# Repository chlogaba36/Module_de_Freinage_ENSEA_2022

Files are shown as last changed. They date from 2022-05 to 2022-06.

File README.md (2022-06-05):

# Module_de_Freinage_ENSEA_2022


<h5>
Dans le cadre de projet de 1ère année à l'ENSEA, nous avons créé un frein pour moteur à courant continue reposant sur le principe de résitance dissipative.
Notre module est alimenté par la source de la MCC et permet via une interface homme-machine de sélectionner les tensions de seuil ainsi que d'avoir un mode manuel.
Sur ce github se trouve les datasheets des éléments utilisés, les éléments de la partie hardware, IHM ainsi que le projet sous STM32CubeIDE.
  
Actuellement, la library de l'écran LCD est complète et fonctionnelle avec une documentation Doxygen, le codeur incrémental et le driver n'ont pas encore été mis en place et le fonctionnement global n'a pas pu être testé.

Pour plus d'information, voir le cahier des charges(disponible dans le dossier livrable)
</h5>

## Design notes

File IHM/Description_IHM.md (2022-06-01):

# Description de la partie IHM:

Ce que nous avons réalisé:
### Commande d'un afficheur LCD Groove avec la carte STM32 Nucleo F410
Cette partie nous a pris beaucoup de temps (dû au manque de documentations, sont manque de qualité et à des librairies partielles en Arduino (à éviter autant que possible).
Ce que nous avons réussi à réaliser:
- Réaliser une connexion I2C (avec les fonctions MX_I2C1_Init, HAL_I2C_IsDeviceReady, HAL_I2C_Master_Transmit
- Refaire une librairie entière pour l'écran LCD qui fonctionne et est documentée.
- Changer des menus (c'est-à-dire afficher plusieurs pattern d'écran).

### Commande d'un bouton sur la carte STM32 Nucleo F410 (fonctionnement sensiblement identique à l'utilisation d'un bouton externe)

### Commande d'un encodeur rotatif avec la carte STM32 Nucleo F410
Cette partie a été partiellement réalisé. Nous avons dans un premier temps pris en main le fonctionnement d'un encodeur, réalisé un premier code pour sa commande, il reste à réaliser la commande encodeur - microprocesseur - afficheur, qui n'est pas encore fonctionnelle.

Par manque de temps, nous avons effectué nos commandes sur la carte STM32 Nucleo F410. Pour passer au microprocesseur STM32G030K6T6, il faudrait changer les connexions (sur les pins et en physique), mais le code est sensiblement le même.
Pour effectuer nos commandes, nous avons utilisé abondamment les fonctions HAL.

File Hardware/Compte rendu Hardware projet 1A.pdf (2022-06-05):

## Compte rendu projet électronique 1A: Partie Hardware

### Contexte – Présentation générale du besoin

L’objectif de ce projet est de réaliser un module de freinage pour une alimentation non réversible (pour une machine à courant continu par exemple).

### Résultats attendus

On réalisera un module de freinage se branchant sur une MCC et s’alimentant avec le secteur.
On prend en contraintes de fonctionnement une tension comprise entre 12 et 48V et un courant de 12A. Le boîtier sera réalisé avec deux emplacements pour des broches bananes 4mm sécurisées respectant la norme IP 3X (protégé contre les corps solides supérieurs à 2.5 mm) pour sécuriser notre module.

Nous cherchons à ouvrir le circuit de l'induit et à le raccorder aux bornes d'une résistance afin que la puissance emmagasinée dans le moteur soit dissipée dans celle-ci au lieu d’être directement stockée dans un condensateur.

En effet, si on coupe l'alimentation de l'induit, le champ étant toujours alimenté, le moteur devient alors une génératrice à excitation séparée qui fonctionne à vide.

En raccordant une résistance R aux bornes de l'induit, la tension induite produit un courant circulant dans le sens inverse dans cette résistance. Il en résulte un couple de freinage d'autant plus grand que ce courant est grand.

La résistance R est choisie pour que que le courant de freinage, soit environ deux fois le courant nominal.

Une interface H/M permettra de sélectionner les valeurs seuils (min et max) de la tension que l’on va réguler par ouverture et fermeture d’une résistance placée en parallèle du circuit; en se déplaçant dans un menu.

Un microprocesseur STM32 communique en utilisant le protocole I2C avec un afficheur.
On considère alors le matériel suivant pour notre projet:
- MOSFET canal N 60V - 3.3V IRFB7530
- Driver de MOSFET
- Résistance de puissance (série E12: 3.9 Ohms; puissance max dissipée: 576W)(P=U²/R)
- Microprocesseur STM32G030K6T6
- Composants RLC
- Display Grove 16*2 LCD ( Tension d’utilisation: 3.3V à 5V; interface I2C)
- Boutons
- Potentiomètre
- Convertisseur BUCK MCP16331T

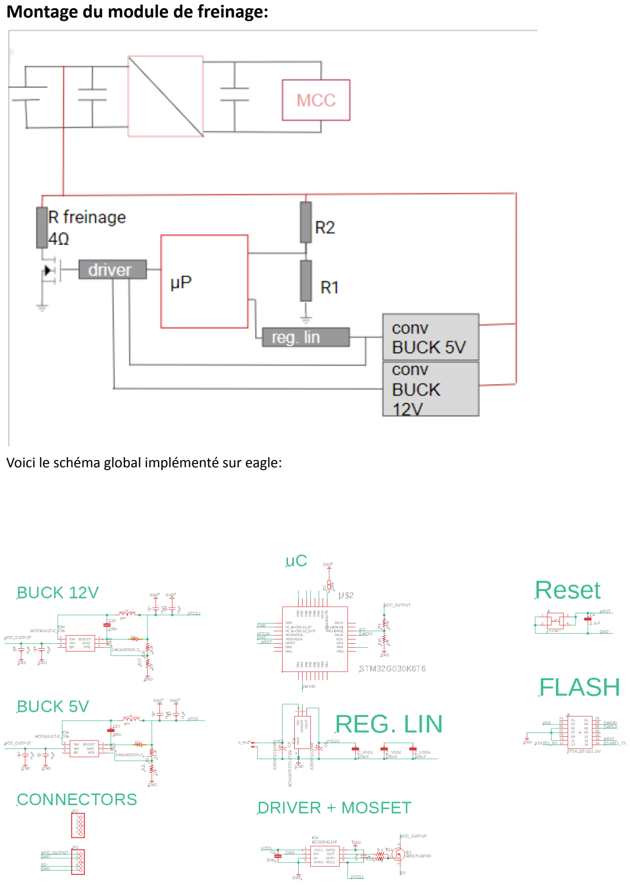
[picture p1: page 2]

### Montage du module de freinage:

Voici le schéma global implémenté sur eagle:

Pour réaliser les schéma eagle il vous faut récupérer les empreintes et le symbole (librairie) des composants snapeda. Nous avons déjà effectué ce travail vous trouverez donc les composants en ouvrant les fichiers eagle sur qui se trouvent sur github. Si vous souhaitez vérifier les composants utilisés pour le convertisseur buck et le driver, il suffit d’ouvrir les datasheet de ces composants pour les récupérer. Nous allons préciser tout cela dans ce qui suit.

S'il est nécessaire d’ ajouter un composant qui n’a pas d’empreinte déjà existante, vous avez la possibilité de créer une empreinte par vous même. Cela n’a pas été notre cas.

Le travail de création de la board complète est entamé mais pour continuer il est nécessaire d'être sûr du fonctionnement des pcb unitaires, voici notre avancement.

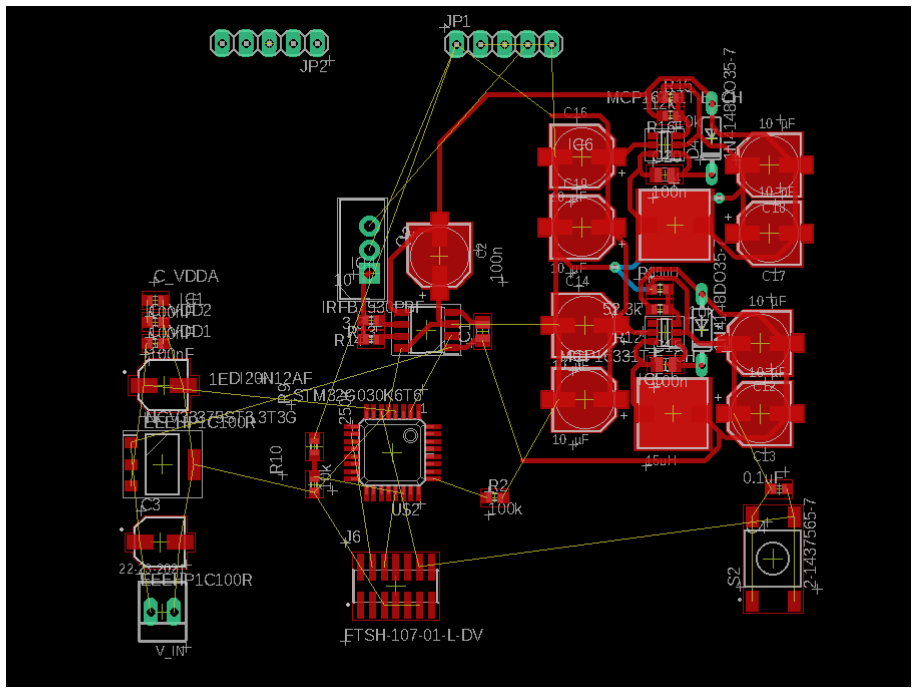
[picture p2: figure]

Ce PCB global est composé de plusieurs parties: Le buck :

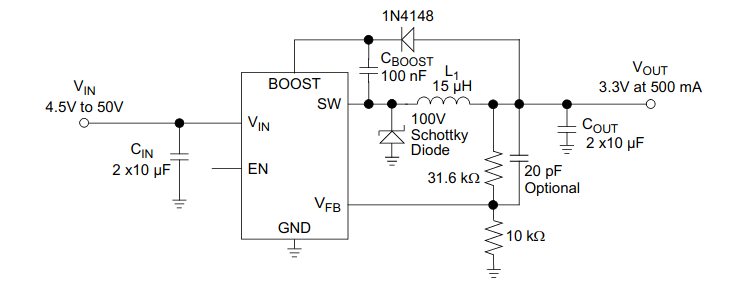
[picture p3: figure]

Résistance de 10kΩ =R1; Résistance de 31,6kΩ= R2. Ces valeurs sont valables si on veut une tension de sortie égale à 3.3V. Or, notre 2e Buck doit avoir 12V en sortie. On doit recalculer R2 de telle sorte que Vfb=0.8V. Voici le détail des calculs.

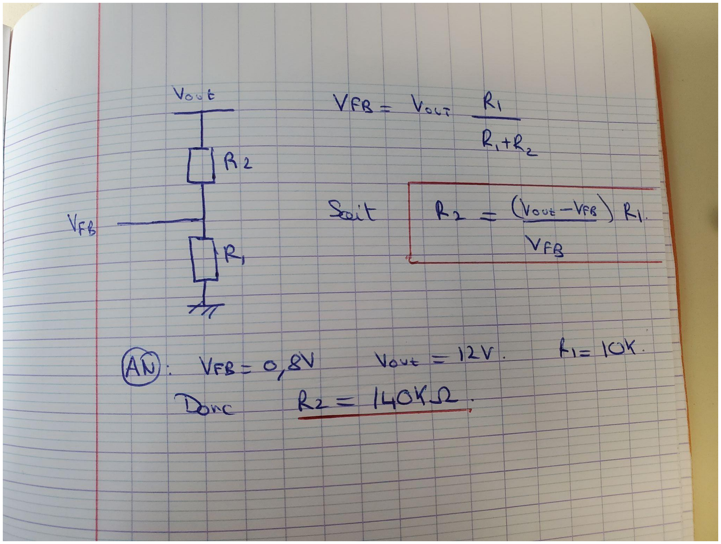
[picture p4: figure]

Pour déterminer R2, on effectue un calcul: On sait que V_fb= 0,8V et V_fb= (R1/R1+R2)*V_out donc R2= R1* (V_out-V_fb)/V_bf

Pour avoir du 5V, R2= 52kΩ

Le PCB est imprimé et soudé.

Le driver: on reproduit le montage trouvé dans la datasheet. Nous avons choisi ce driver car c’est celui qui doit être associé au transistor Mosfet.

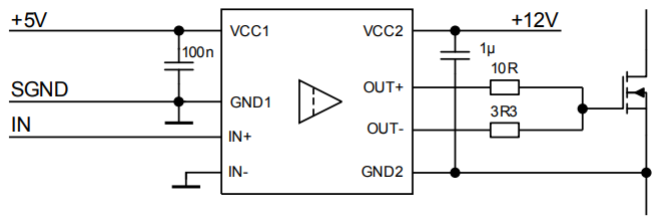
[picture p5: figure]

le PCB est imprimé il faut le souder et le tester.

Sonde de tension:

Elle nous permet de prélever la tension en sortie de la MCC afin de déterminer l’ouverture ou la fermeture du circuit de décharge à l’aide d’un traitement numérique effectué par le microprocesseur.

Étant donné que ce dernier n’admet qu’une tension max de 3,3V, et que la tension en sortie de la MCC peut atteindre un pic de 80V, on cherche à passer de 80 V à 3,3V on utilise pour cela un pont diviseur de tension, de coefficient 1/25.

Au départ nous voulions utiliser un pont diviseur de tension suivi d’un suiveur (impédance d’entrée infinie) pour que les résistances soient considérées en série mais finalement, compte tenu de l'impédance d’entrée du microprocesseur très élevée, on n’utilise pas d’AOP (montage suiveur)avec R1=250kΩ et R2=10kΩ.
Le choix de résistances d’un ordre de grandeur du kΩ nous permet de bien dissiper la chaleur.

Modification Diviseur de tension :

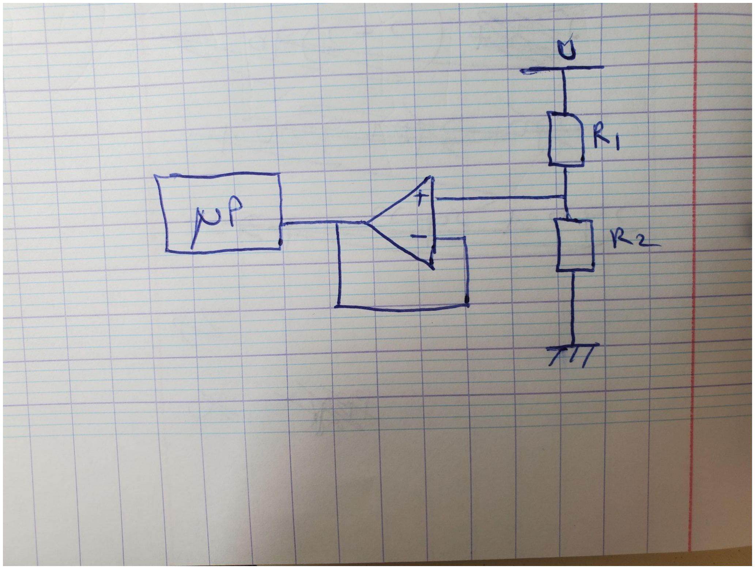
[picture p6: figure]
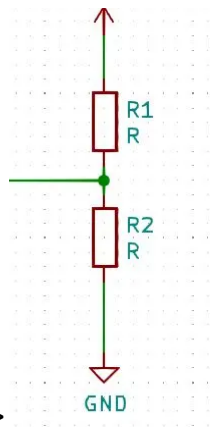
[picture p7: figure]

<=>

Résumé de la partie hardware:
- PCB unitaires réalisés sous eagle.
- PCB Global bien entamé.
- PCB unitaire buck en test.
- Il reste à souder et tester le PCB driver plus Mos, terminer le PCB global (déjà entamé).

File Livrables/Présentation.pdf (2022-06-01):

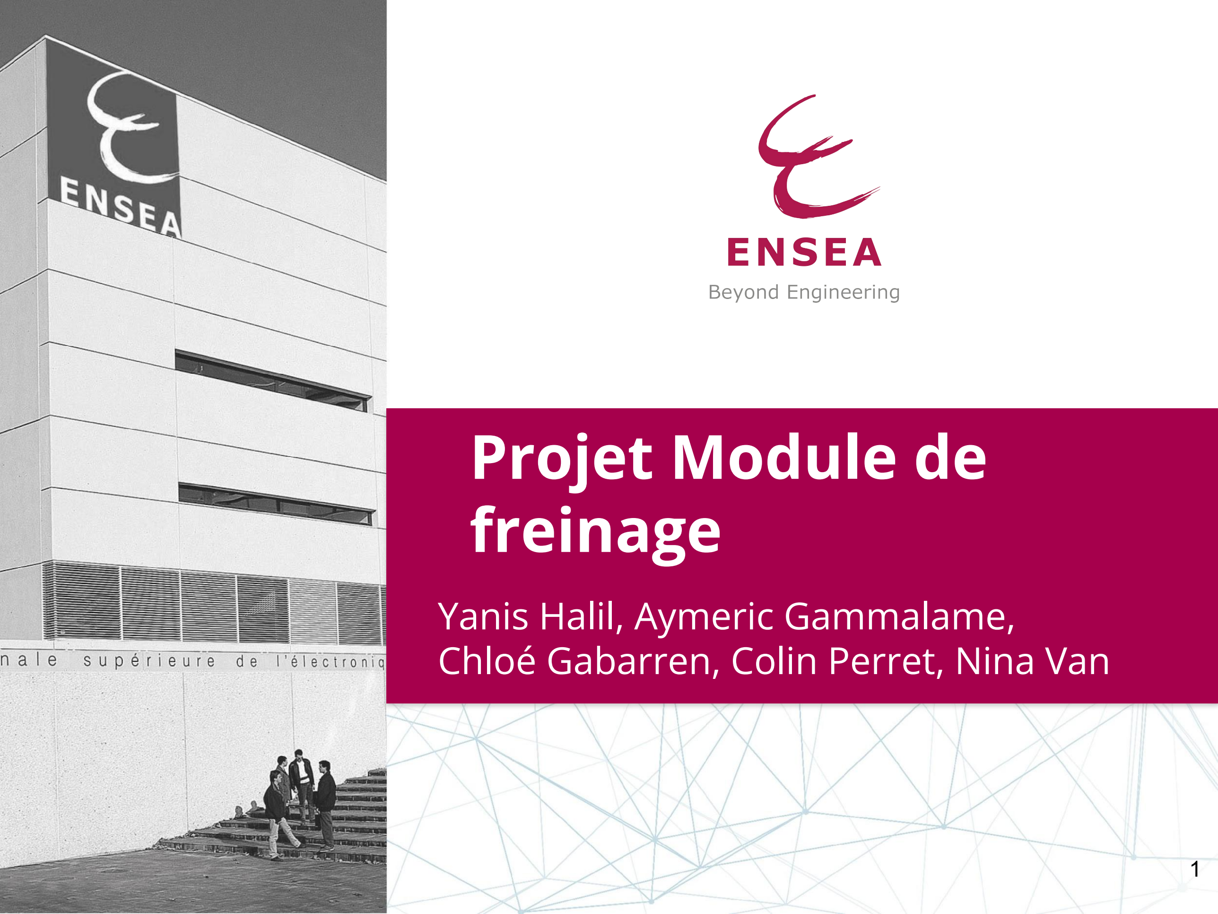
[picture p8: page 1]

Yanis Halil, Aymeric Gammalame,

# Chloé Gabarren, Colin Perret, Nina Van

# Projet Module de freinage

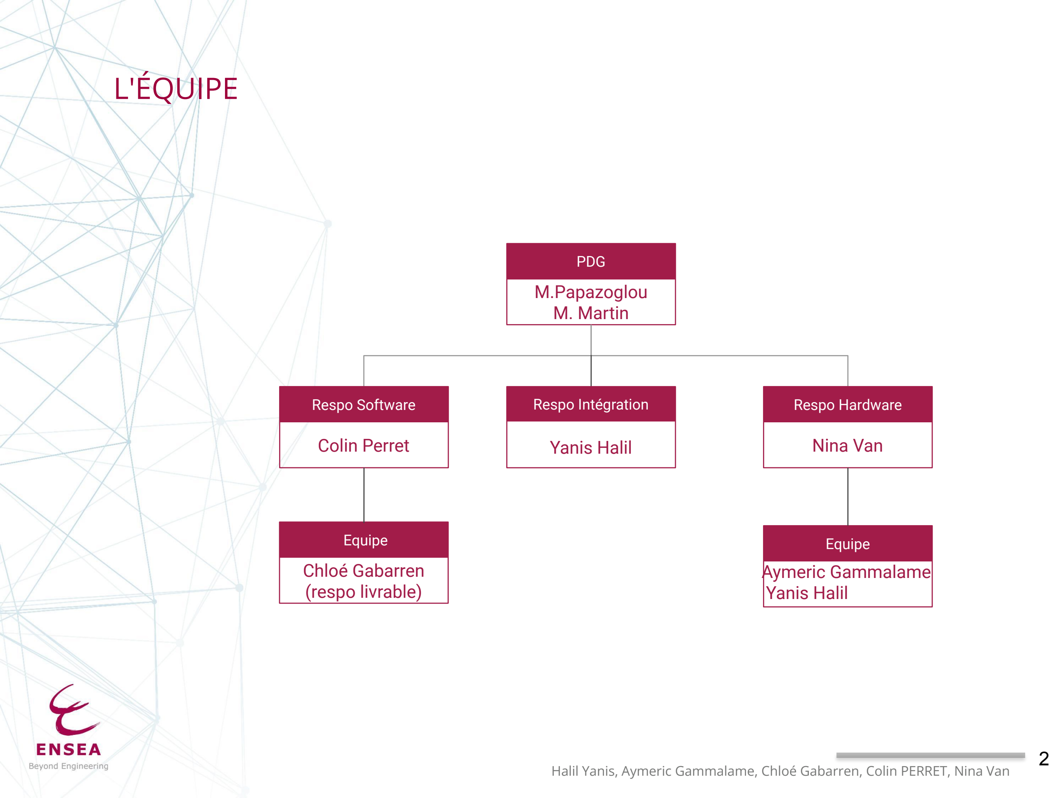
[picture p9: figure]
L'ÉQUIPE; M.Papazoglou M. Martin; Respo Software; Colin Perret; Equipe; Chloé Gabarren (respo livrable); Respo Hardware; Nina Van; Equipe Aymeric Gammalame Yanis Halil; PDG; Yanis Halil; Respo Intégration

Halil Yanis, Aymeric Gammalame, Chloé Gabarren, Colin PERRET, Nina Van

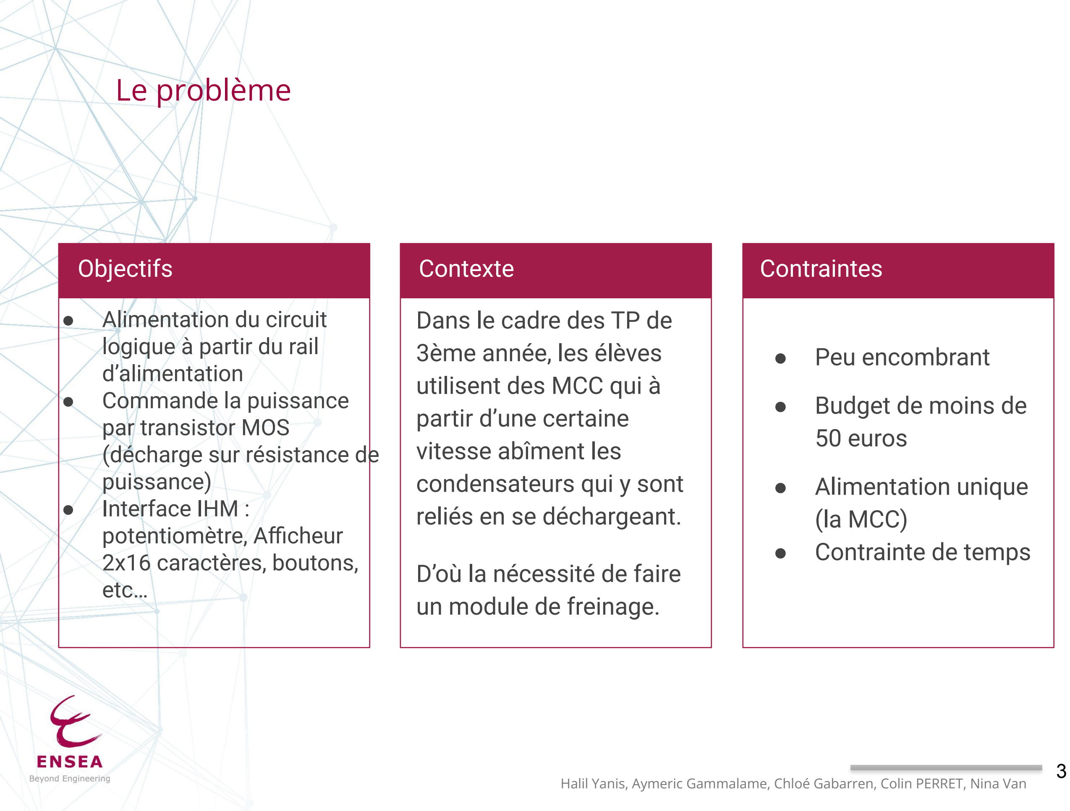
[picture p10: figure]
Objectifs; ● Alimentation du circuit logique à partir du rail d’alimentation ● Commande la puissance par transistor MOS (décharge sur résistance de puissance) ● Interface IHM : potentiomètre, Afficheur 2x16 caractères, boutons, etc…; Contexte; Dans le cadre des TP de 3ème année, les élèves utilisent des MCC qui à partir d’une certaine vitesse abîment les condensateurs qui y sont reliés en se déchargeant.; D’où la nécessité de faire un module de freinage.; Contraintes; ● Peu encombrant; ● Budget de moins de 50 euros; ● Alimentation unique (la MCC) ● Contrainte de temps; Le problème

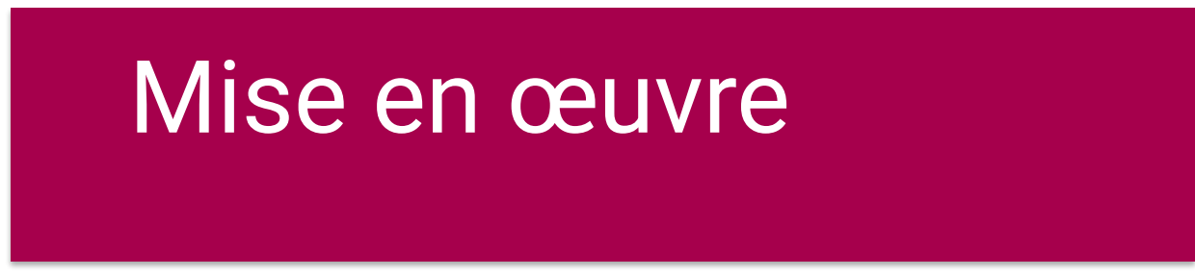
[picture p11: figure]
Mise en œuvre

### - Introduction au projet - Séance de réflexion

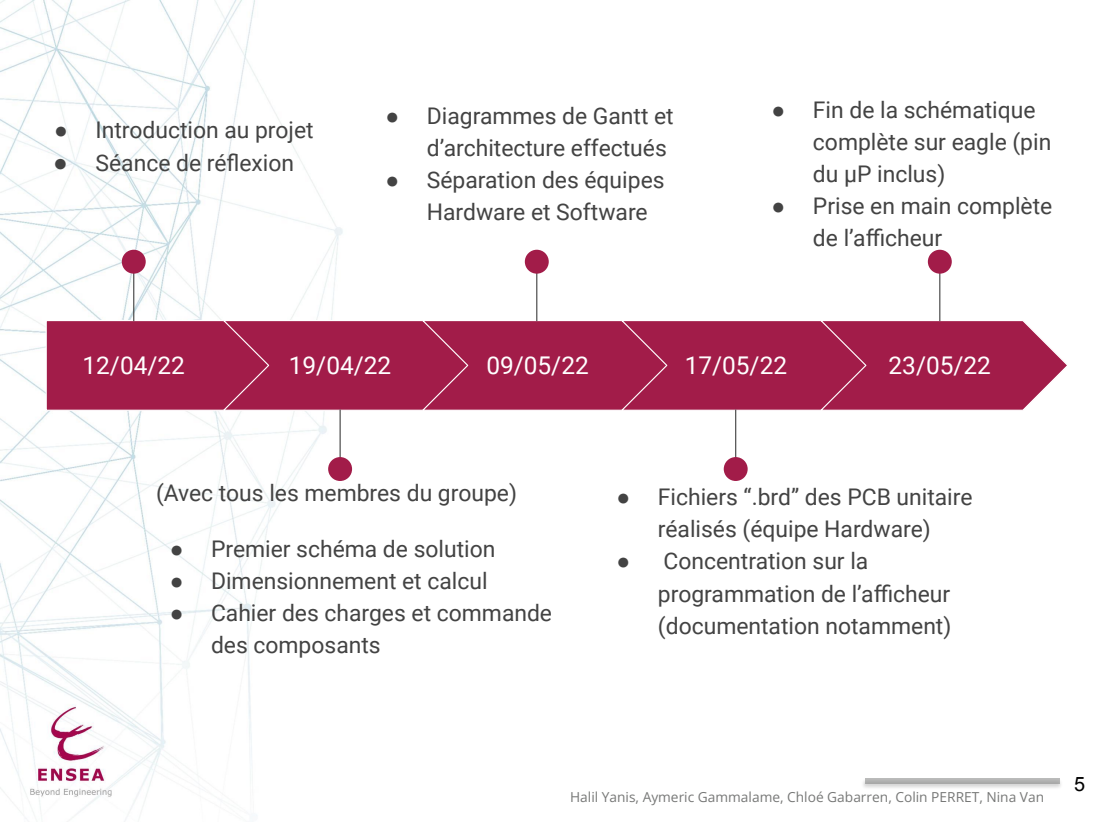
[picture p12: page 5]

● Fin de la schématique
complète sur eagle (pin
du µP inclus)
● Prise en main complète
de l’afficheur

● Diagrammes de Gantt et
d’architecture effectués
● Séparation des équipes
Hardware et Software

(Avec tous les membres du groupe)

● Fichiers “.brd” des PCB unitaire
réalisés (équipe Hardware)
● Concentration sur la
programmation de l’afficheur
(documentation notamment)

● Premier schéma de solution
● Dimensionnement et calcul
● Cahier des charges et commande
des composants

# Diagramme d’architecture

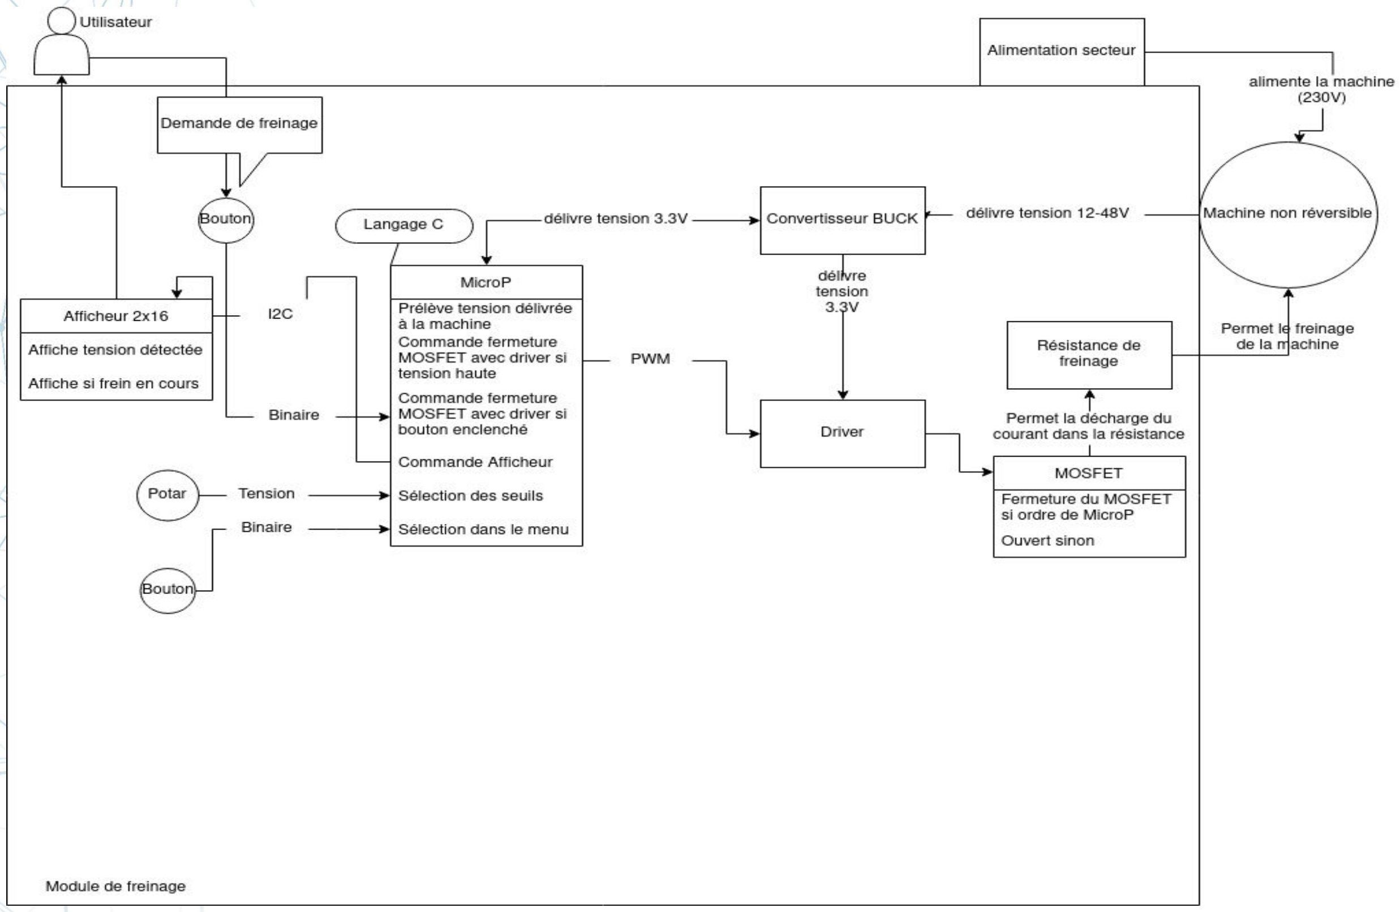
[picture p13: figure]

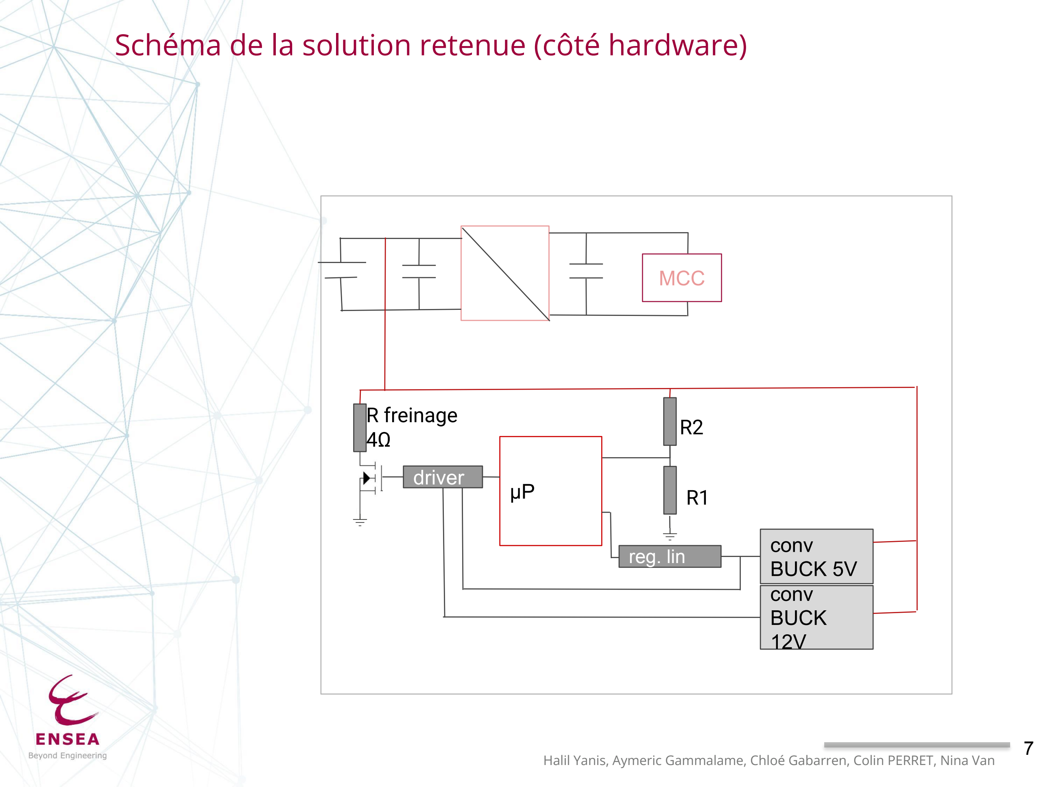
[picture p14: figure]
MCC; driver; conv BUCK 5V; reg. lin; conv BUCK 12V; R freinage 4Ω

# Schéma de la solution retenue (côté hardware)

# Schématique globale

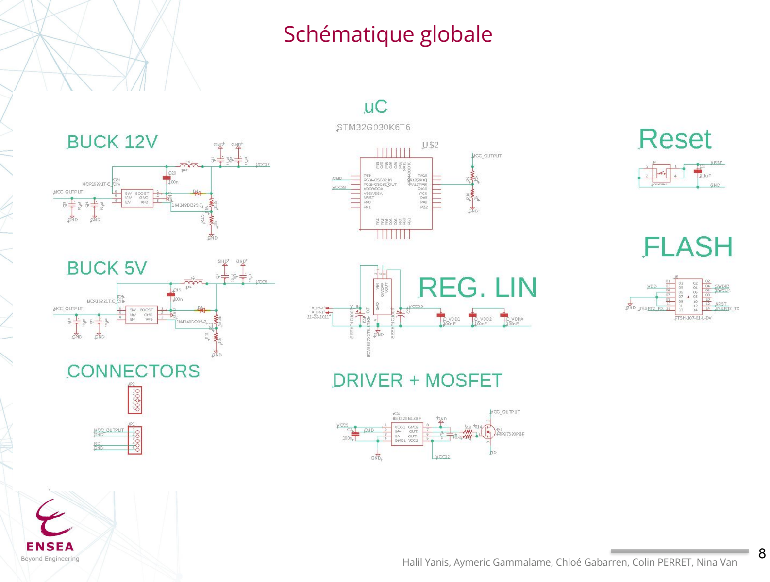
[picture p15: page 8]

Halil Yanis, Aymeric Gammalame, Chloé Gabarren, Colin PERRET, Nina Van 8

# PCB unitaires: Driver + MOSFET

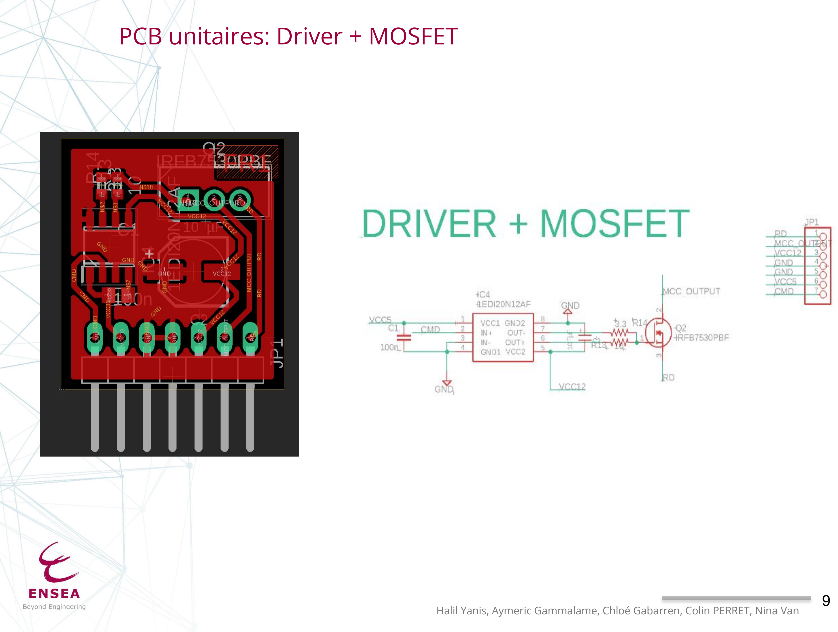
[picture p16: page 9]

Halil Yanis, Aymeric Gammalame, Chloé Gabarren, Colin PERRET, Nina Van 9

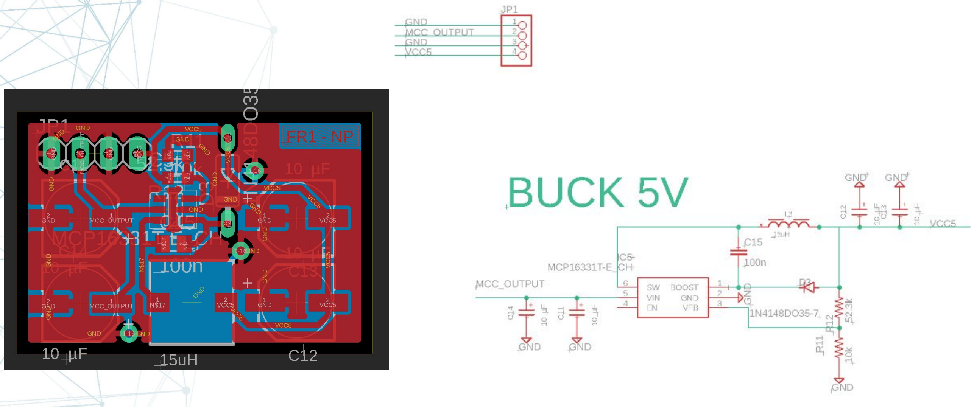
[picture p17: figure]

Halil Yanis, Aymeric Gammalame, Chloé Gabarren, Colin PERRET, Nina Van 10

# PCB unitaires: convertisseur Buck

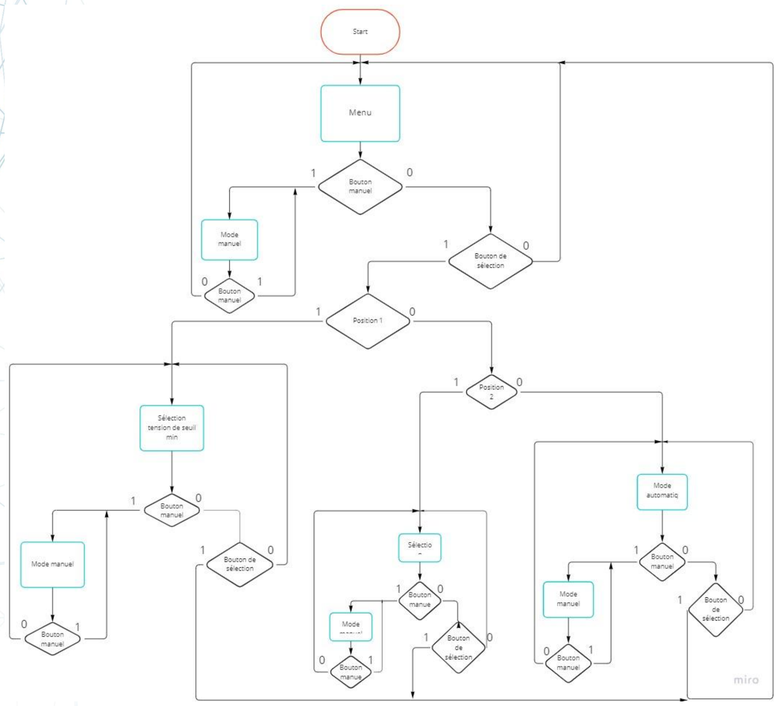
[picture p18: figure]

Halil Yanis, Aymeric Gammalame, Chloé Gabarren, Colin PERRET, Nina Van 11

# Diagramme de fonctionnement du software

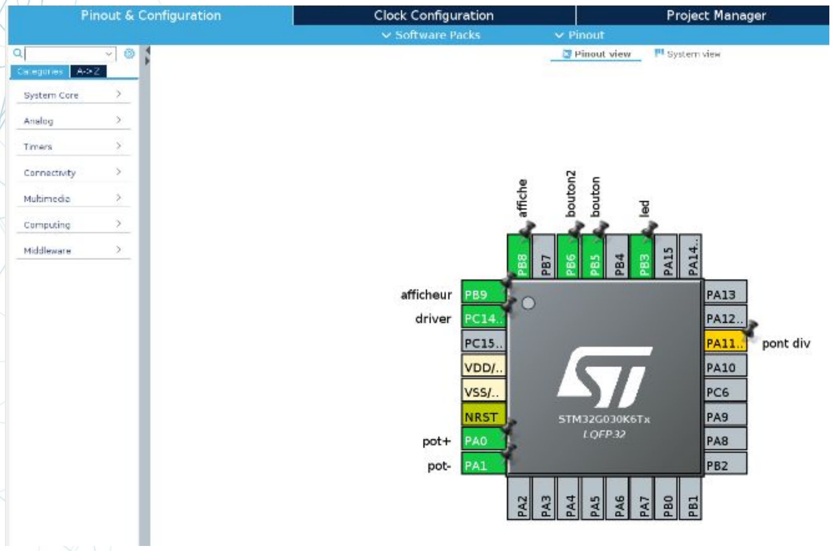
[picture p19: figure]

Halil Yanis, Aymeric Gammalame, Chloé Gabarren, Colin PERRET, Nina Van 12

# Configuration du microprocesseur sur STM32 CubeIDE

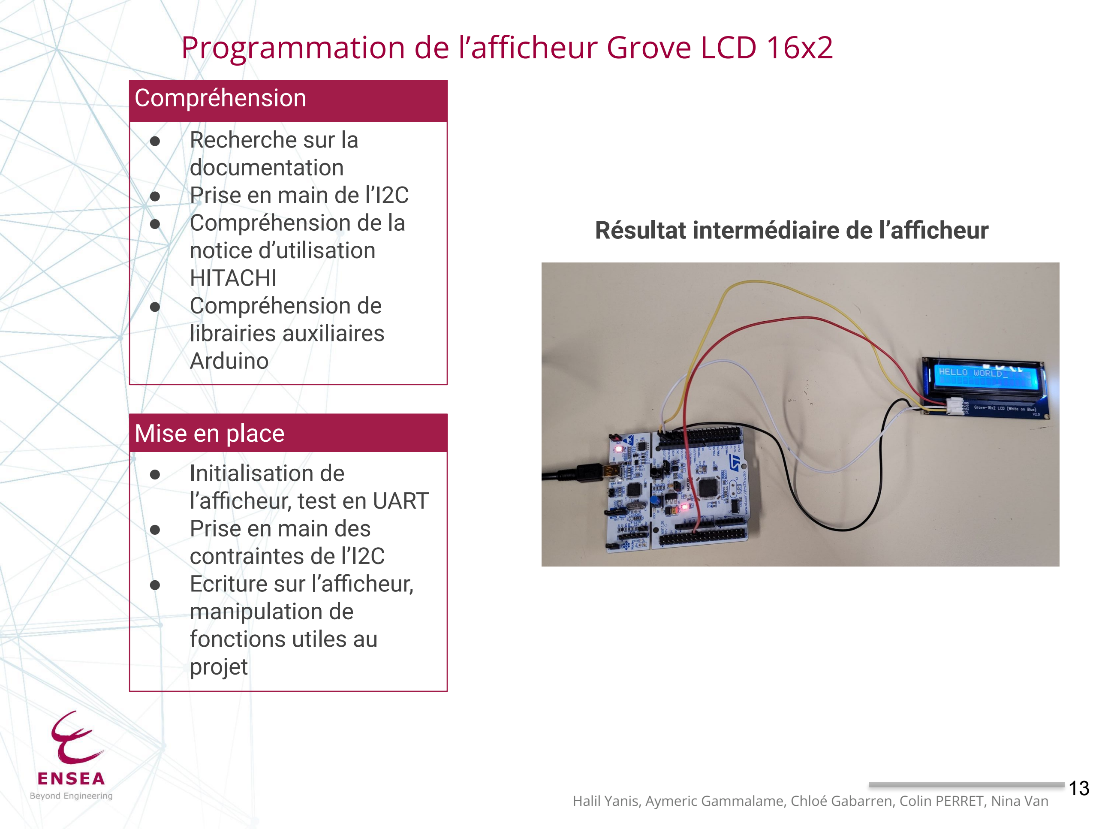
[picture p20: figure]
Compréhension; Mise en place; ● Recherche sur la documentation ● Prise en main de l’I2C ● Compréhension de la notice d’utilisation HITACHI ● Compréhension de librairies auxiliaires Arduino; ● Initialisation de l’afficheur, test en UART ● Prise en main des contraintes de l’I2C ● Ecriture sur l’afficheur, manipulation de fonctions utiles au projet; Résultat intermédiaire de l’afficheur

Halil Yanis, Aymeric Gammalame, Chloé Gabarren, Colin PERRET, Nina Van 13

# Programmation de l’afficheur Grove LCD 16x2

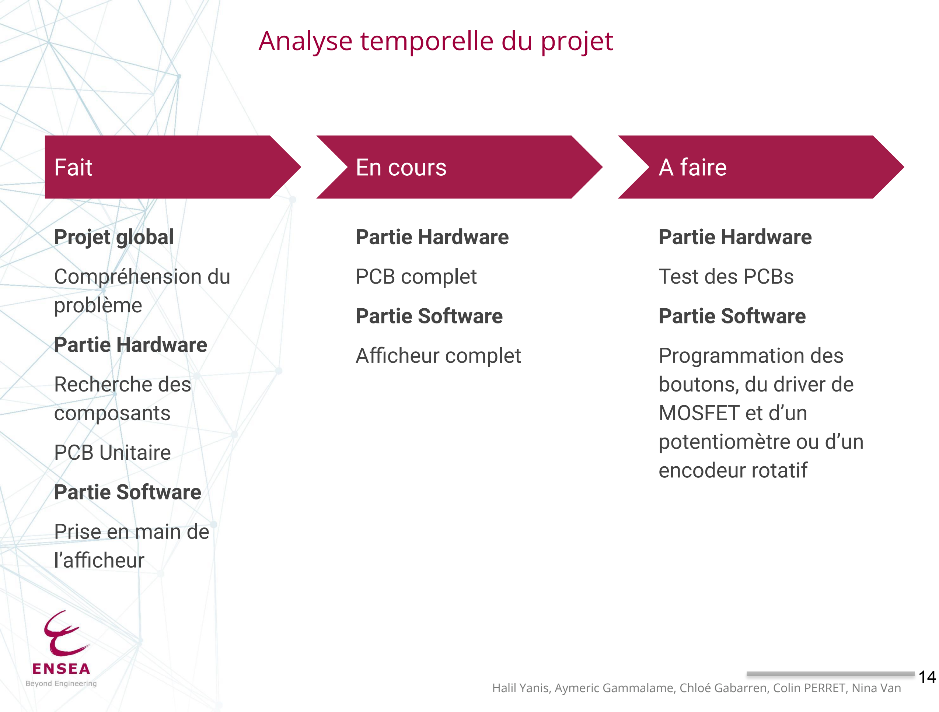
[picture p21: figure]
Fait; Projet global; Compréhension du problème; Partie Hardware; Recherche des composants; PCB Unitaire; Partie Software; Prise en main de l’afficheur; En cours; PCB complet; Afficheur complet; A faire; Test des PCBs; Programmation des boutons, du driver de MOSFET et d’un potentiomètre ou d’un encodeur rotatif; Analyse temporelle du projet

Halil Yanis, Aymeric Gammalame, Chloé Gabarren, Colin PERRET, Nina Van 14

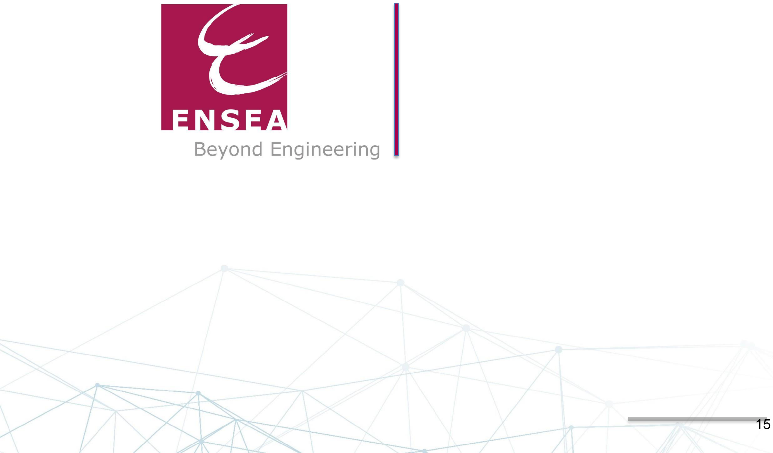
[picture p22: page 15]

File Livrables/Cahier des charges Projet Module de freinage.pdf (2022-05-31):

## Cahier des charges : Projet Module de freinage

### Contexte – Présentation générale du besoin

L’objectif de ce projet est de réaliser un module de freinage pour une alimentation non réversible (pour une machine à courant continu par exemple).

### Résultats attendus

On réalisera un module de freinage se branchant sur une MCC et s’alimentant avec le secteur.
On prend en contraintes de fonctionnement une tension comprise entre 12 et 48V et un courant de 12A.
On réalisera un boîtier avec deux emplacements pour des broches bananes 4mm sécurisées respectant la norme IP 3X (protégé contre les corps solides supérieurs à 2.5 mm) pour sécuriser notre module.

On cherche à ouvrir le circuit de l'induit et à le raccorder aux bornes d'une résistance afin que la puissance emmagasinée dans le moteur soit dissipée dans celle-ci au lieu d’être directement stockée dans un condensateur.

En effet, si on coupe l'alimentation de l'induit, le champ étant toujours alimenté, le moteur devient alors une génératrice à excitation séparée qui fonctionne à vide.

En raccordant une résistance R aux bornes de l'induit, la tension induite produit un courant circulant dans le sens inverse dans cette résistance. Il en résulte un couple de freinage d'autant plus grand que ce courant est grand.

La résistance R est choisie pour que que le courant de freinage, soit environ deux fois le courant nominal.

Une interface H/M permettra de sélectionner les valeurs seuils (min et max) de la tension que l’on va réguler par ouverture et fermeture d’une résistance placée en parallèle du circuit; en se déplaçant dans un menu.

Un microprocesseur STM32 communique en utilisant le protocole I2C avec un afficheur. Pour l’interface H/M, nous avons besoin de:
- 1 afficheur 2x16
- 2 boutons
- 1 potentiomètre

On considère alors le matériel suivant pour notre projet:
- MOSFET canal N 60V - 3.3V
- Driver de MOSFET correspondant au MOSFET
- Résistance de puissance (série E12: 2 Ohms; puissance max dissipée: 1152W)
- Microprocesseur STM32G030K6T6
- Composants RLC

- Display Grove 16*2 LCD ( Tension d’utilisation: 3.3V à 5V; interface I2C)
- Boutons
- Potentiomètre

### Montage du module de freinage

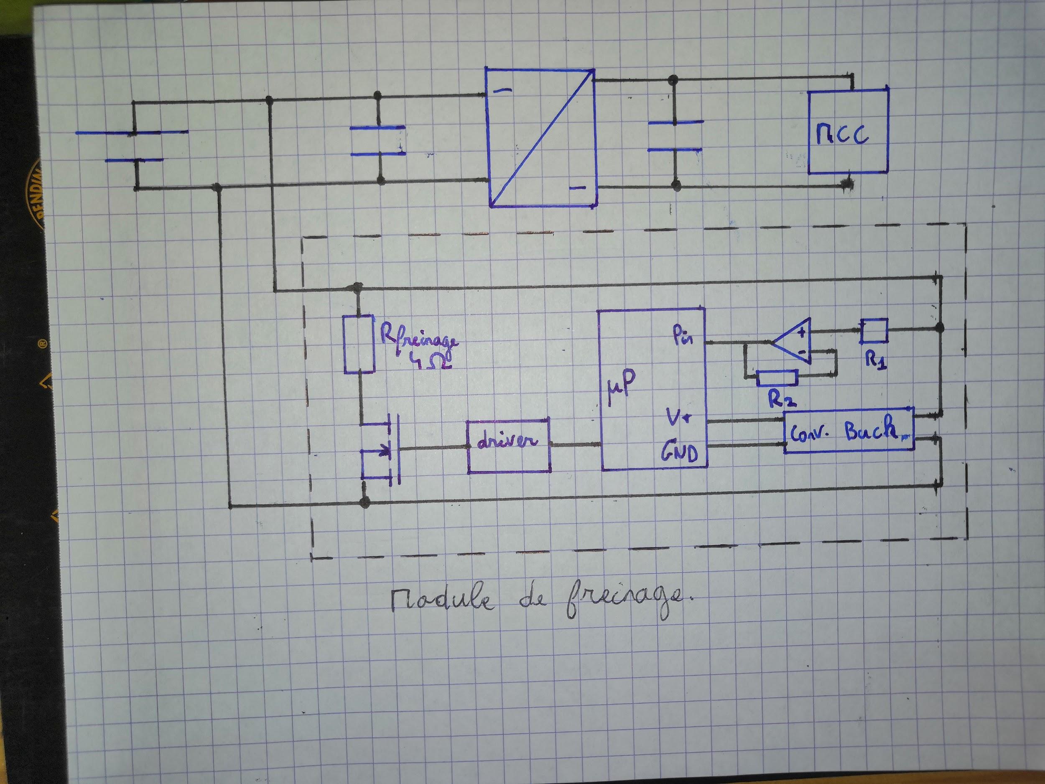
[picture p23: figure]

### Informations complémentaires

Contraintes de planning
On s’attachera à respecter le planning suivant:
12/04/22 : Début du projet
19/04/22: Commande de composants effectuée et cahier des charges complété 09/05/22 : Diagrammes de Gantt et d’architecture effectués
17/05/22 : PCB unitaire réalisé
24/05/22 : PCB complet réalisé
01/06/22 : Fin du projet

Contraintes de budget
On se limitera à un budget de 50€.

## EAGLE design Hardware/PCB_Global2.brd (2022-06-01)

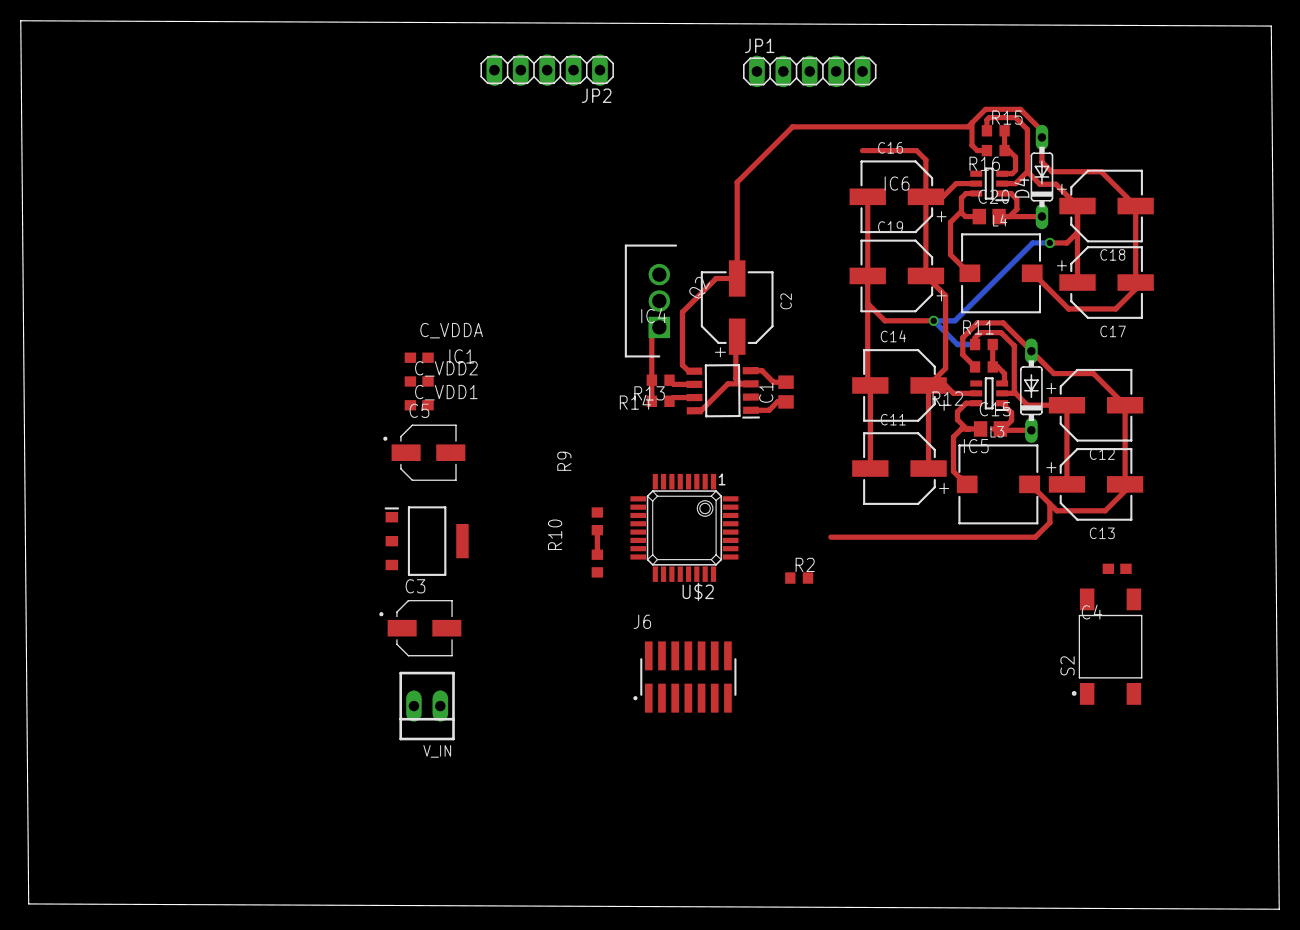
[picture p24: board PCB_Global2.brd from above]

Board: 2 copper layers, 121.1 x 85.5 mm, 42 parts (0 on the bottom side), 23 nets.

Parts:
C1, C15, C20: 100n; C0805
C2, C11, C12, C13, C14, C16, C17, C18, C19: 10 µF; WCAP-ASLI_6.3X7.7(DXL)
C3, C5: EEEHP1C100R; CAP_EEEHP1C100R
C4: 0.1uF; C0603
C_VDD1, C_VDD2: 100nF; C0603
C_VDDA: 100nF; C0603
D3, D4: 1N4148DO35-7; DO35-7
IC1: NCV33375ST3.3T3G; SOT230P700X175-4N
IC4: 1EDI20N12AF; SOIC127P600X175-8N
IC5, IC6: MCP16331T-E_CH; SOT95P280X145-6N
J6: FTSH-107-01-L-DV; SAMTEC_FTSH-107-01-L-DV
JP1, JP2: 1X05
L3, L4: 15uH; WE-PD_7345R
Q2: IRFB7530PBF; TO254P483X1016X1994-3P
R2: 100k; R0603
R9: 250k; R0603
R10, R11, R15: 10k; R0603
R12: 52.3k; R0603
R13: 10; R0603
R14: 3.3; R0603
R16: 112k; R0603
S2: 2-1437565-7; SW_2-1437565-7
U$2: STM32G030K6T6; QFP32_STM32
V_IN: 22-23-2021

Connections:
CMD: IC4.2, U$2.2
GND: C2.1, C3.2, C4.2, C5.2, C11.2, C12.1, C13.1, C14.2, C16.2, C17.1, C18.1, C19.2, C_VDD1.2, C_VDD2.2, C_VDDA.2, IC1.4, IC4.3, IC4.8, IC5.2, IC6.2, J6.05, J6.07, J6.11, JP1.2, JP1.5, R2.2, R10.1, R11.1, R15.1, S2.1, S2.2, U$2.5, V_IN.1
I2C: R9.1, R10.2, U$2.22
MCC_OUTPUT: C11.1, C14.1, C16.1, C19.1, IC5.5, IC6.5, JP1.1, Q2.2, R9.2
unnamed: IC4.6, R13.1
unnamed: IC4.7, R14.1
unnamed: C_VDD2.1, C_VDDA.1
unnamed: C1.2, IC4.4
unnamed: R2.1, U$2.25
unnamed: C15.1, IC5.6, L3.1
unnamed: Q2.1, R13.2, R14.2
unnamed: C15.2, D3.C, IC5.1
unnamed: IC5.3, R11.2, R12.1
unnamed: C20.1, IC6.6, L4.1
unnamed: C20.2, D4.C, IC6.1
unnamed: IC6.3, R15.2, R16.1
NRST: C4.1, J6.12, S2.3, S2.4, U$2.6
RD: JP1.4, Q2.3
SWCLK: J6.06, U$2.21
SWDIO: J6.04, U$2.10
VCC5: C1.1, C3.1, C12.2, C13.2, D3.A, IC1.1, IC4.1, L3.2, R12.2, V_IN.2
VCC12: C2.2, C17.2, C18.2, D4.A, IC4.5, L4.2, R16.2
VCC33: C5.1, C_VDD1.1, IC1.3, U$2.4

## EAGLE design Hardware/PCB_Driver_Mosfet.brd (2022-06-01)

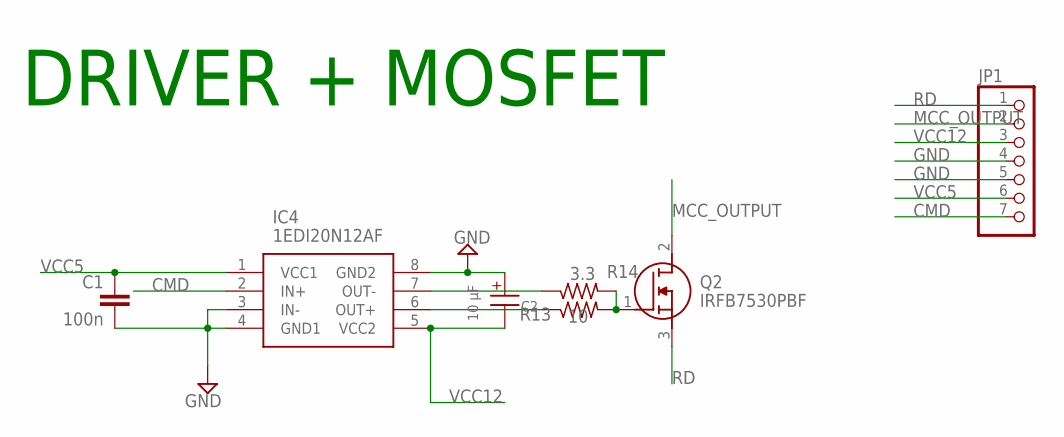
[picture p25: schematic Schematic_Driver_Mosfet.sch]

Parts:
C1: 100n; C0805
C2: 10 µF; WCAP-ASLI_6.3X7.7(DXL)
IC4: 1EDI20N12AF; SOIC127P600X175-8N
JP1: PINHD-1X7/90; 1X07/90
Q2: IRFB7530PBF; TO254P483X1016X1994-3P
R13: 10; R0603
R14: 3.3; R0603

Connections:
CMD: IC4.2 (IN+), JP1.7
GND: C2.1 (+), IC4.3 (IN-), IC4.8 (GND2), JP1.4, JP1.5
MCC_OUTPUT: JP1.2, Q2.2 (D)
unnamed: IC4.6 (OUT+), R13.1
unnamed: IC4.7 (OUT-), R14.1
unnamed: C1.2, IC4.4 (GND1)
unnamed: Q2.1 (G), R13.2, R14.2
RD: JP1.1, Q2.3 (S)
VCC12: C2.2 (-), IC4.5 (VCC2), JP1.3
VCC33: C1.1, IC4.1 (VCC1), JP1.6

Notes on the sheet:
DRIVER + MOSFET

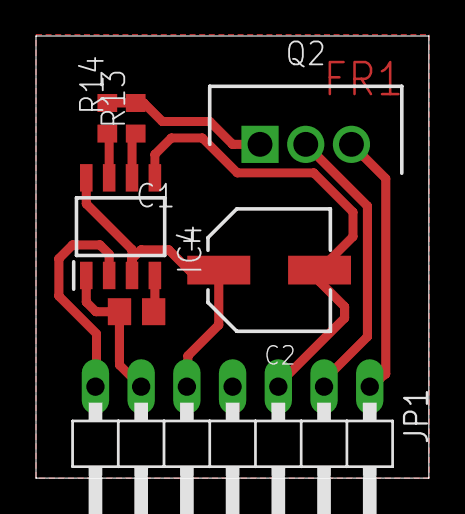
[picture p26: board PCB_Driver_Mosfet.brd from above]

Board: 2 copper layers, 21.8 x 24.6 mm, 7 parts (0 on the bottom side), 10 nets.

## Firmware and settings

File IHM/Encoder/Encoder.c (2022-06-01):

/**
 *\file Encoder.c
 *\brief Librairie faites pour utiliser l'encodeur selon nos besoins.
 *\author Chloé GABARREN et Colin PERRET
 *\version 1.0
 *\date 31/05/2022
 *
 * Ensemble des fonctions qui seront utilisé pour notre usage de l'encodeur,
 * donc pour la sélection dans le menu et modifier la valeur des tensions seuils.
 *
 */

/*
	vmin : menu = 0
	vmax : menu = 1
	mode auto : menu = 2
	mode manuel : menu = 3
 */
#include "Encoder.h"
TIM_HandleTypeDef htim1;

/**
 * \fn void Encoder_Start(void)
 * \brief Fonction permettant d'initialiser l'encodeur.
 * \param void
 * \return void.
 */
void Encoder_Start(void){
	HAL_TIM_Encoder_Start(&htim1, TIM_CHANNEL_ALL);
}

/**
 * \fn void Encoder_Reset(int past_incremental_val, int current_incremental_val)
 * \brief Fonction permettant de réinitialiser la valeur lu sur l'encodeur.
 * \param Les valeurs passé et présente lu sur l'encodeur.
 * \return void.
 */
void Encoder_Reset(int past_incremental_val, int current_incremental_val){
	past_incremental_val = __HAL_TIM_SET_COUNTER(&htim1,32767);
	current_incremental_val = __HAL_TIM_SET_COUNTER(&htim1,32767);
}

/**
 * \fn void Encoder_Count(int* incremental_val)
 * \brief Fonction permettant de mettre à jour les valeurs passé et présente de l'encodeur.
 * \param Le tableau contenant les valeurs passé et présente de l'encodeur.
 * \return void.
 */
void Encoder_Count(int* incremental_val){
	int current_incremental_val = __HAL_TIM_GET_COUNTER(&htim1);
	incremental_val[1] = incremental_val[0];
	incremental_val[0] = current_incremental_val;
}

/**
 * \fn void Encoder_Delta(int* incremental_val)
 * \brief Fonction permettant de mettre à jour les valeurs passé et présente de l'encodeur.
 * \param Le tableau contenant les valeurs passé et présente de l'encodeur.
 * \return La différence.
 */
int Encoder_Delta(int* incremental_val){
	int delta = incremental_val[0]-incremental_val[1];
	return delta;
}

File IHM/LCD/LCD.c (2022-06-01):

/**
 *\file LCD.c
 *\brief Librairie faites sur mesure pour controler l'écran LCD
 *\author Colin PERRET et Chloé GABARREN
 *\version 1.1
 *\date 31/05/2022
 *
 * Ensemble des fonctions qui seront utilisé pour écrire sur l'afficheur.
 * Cette librairie est plus digest et plus détaillé que celles disponibles
 * sur internet et celle mise à disposition par le fabricant.
 *
 */

#include <LCD.h>

I2C_HandleTypeDef hi2c1;

/**
 * \fn void LCD_transmit_cmd (char cmd)
 * \brief Fonction de transfert d'une commande à l'écran.
 *        Le microcontroleur faisant interface entre l'I2C et
 *        l'écran fonctionne sur 10 bits. Le MSB est obtenue
 *        par transfert d'une première information qui est soit
 *        0x40 pour afficher un caractère ou 0x80 pour une
 *        commande permettant par exemple d'allumer l'écran,
 *        déplacer le curseur ou l'écran, etc (voir datasheet
 *        HD44780U page 24). Le bit suivant est un bit lié au
 *        protocol I2C dont on n'a pas à se soucier et il reste
 *        l'octet de donnée (le caractère en ASCII ou une commande).
 * \param un caractère car c'est une information codé sur un
 *        octet.
 * \return void.
 */

void LCD_transmit_cmd(char cmd){
   char data[2] = {0x80,cmd};
   HAL_I2C_Master_Transmit(&hi2c1, LCD_ADDRESS<<1, data, sizeof(data), HAL_MAX_DELAY);
}

/**
 * \fn void LCD_Init (void)
 * \brief Fonction pour initialiser l'écran.
 *        Reproduit les étapes de la datasheet HD44780U page 45.
 * \param void.
 * \return void.
 */
void LCD_Init(void){
   //init begin
   HAL_Delay(50);
   LCD_transmit_cmd(LCD_SET);
   HAL_Delay(5);
   LCD_transmit_cmd(LCD_SET);
   HAL_Delay(1);
   LCD_transmit_cmd(LCD_SET);
   HAL_Delay(1);
   //trois set
   LCD_transmit_cmd(LCD_SET3C);
   HAL_Delay(5);
   LCD_transmit_cmd(LCD_DISPOFF);
   HAL_Delay(5);
   LCD_transmit_cmd(LCD_DISPCLEAR);
   HAL_Delay(5);
   LCD_transmit_cmd(LCD_MODESET);
   HAL_Delay(5);
   //init finished

   LCD_Home();
   LCD_transmit_cmd(LCD_DISPONF);
   HAL_Delay(5);
   LCD_transmit_cmd(LCD_MODESET);
   HAL_Delay(2000);
}

/**
 * \fn void LCD_set_Cursor(int ligne, int colonne)
 * \brief Fonction pour placer le cursor à la ligne et la
 *        colonne placé en argument (les indices commencent à 0).
 * \param Les entiers ligne et colonne dont les indices commencent à 0.
 * \return void.
 */
void LCD_set_Cursor(int ligne, int colonne){
   char pos;
   if (colonne==1){
      pos = 0x40 | ( (char) ligne);
   }
   else{
      pos = (char) ligne;
   }
   LCD_transmit_cmd(pos);
   HAL_Delay(1);
}

/**
 * \fn void LCD_PrintChar(char c)
 * \brief Fonction permettant d'afficher un caractère.
 *        Comme mentionné dans la fonction "LCD_Transmit_cmd",
 *        Il faut d'abord envoyé l'information au microcontrolleur
 *        de l'écran que l'on veut écrire un caractère avant de l'envoyer.
 * \param Le caractère que l'on veut écrire.
 * \return void.
 */
void LCD_PrintChar(char c){
   char data[2] = {0x40,c};
   HAL_I2C_Master_Transmit(&hi2c1, LCD_ADDRESS<<1, data, sizeof(data), HAL_MAX_DELAY);
   HAL_Delay(5);
}

/**
 * \fn void LCD_PrintChar(char* str, int len)
 * \brief Fonction permettant d'afficher une chaine de caractères en connaissant sa taille.
 *        On réalise une boucle for pour envoyer caractère par caractère avec l'information
 *        que l'on va écrire un caractère sur l'écran comme mentionné dans "LCD_PrintChar".
 *
 *        Remarque: on peut envoyer directement "@X...X", le @ correspond à 0x40 suivi de la
 *                  chaine de caractères.
 * \param La chaine de caractères que l'on veut écrire ainsi que sa taille.
 * \return void.
 */
void LCD_PrintStr(char* str, int len){
   int i=0;
   for (i=0;i<len;i++){
      char data[2] = {0x40,str[i]};
      HAL_I2C_Master_Transmit(&hi2c1, LCD_ADDRESS<<1, data, sizeof(data), HAL_MAX_DELAY);
      HAL_Delay(5);
   }
}

/**
 * \fn void LCD_Home(void)
 * \brief Fonction permettant de replacer l'écran et le cursor en haut à gauche.
 * \param void.
 * \return void.
 */
void LCD_Home(void){
   LCD_transmit_cmd(LCD_HOME);
   HAL_Delay(5);
}

/**
 * \fn void LCD_Clear(void)
 * \brief Fonction permettant d'effacer tous ce qui est écrit sur l'écran.
 * \param void.
 * \return void.
 */
void LCD_Clear(void){
   LCD_transmit_cmd(LCD_DISPCLEAR);
   HAL_Delay(5);
}

/**
 * \fn void LCD_YNCursorBlink(int i)
 * \brief Fonction permettant de faire clignoter le curseur.
 * \param Un entier (1 ou 0) pour faire clignoter le curseur ou pas.
 * \return void.
 */
void LCD_YNCursorBlink(int i){
   if (i==1){
      LCD_transmit_cmd(0x0f);
      HAL_Delay(5);
   }
   else {
      LCD_transmit_cmd(0x0e);
      HAL_Delay(5);
   }
}

/**
 * \fn void LCD_Manuel(void)
 * \brief Fonction permettant d'afficher le passage en mode manuel.
 *        Piste d'amélioration: on affiche également la tension mesuré.
 * \param void.
 * \return void.
 */
void LCD_Manuel(void){
   LCD_Clear();
   LCD_Home();
   char str[14]="Mode manuel ON";
   LCD_PrintStr(str,14);
}

/**
 * \fn void LCD_PrintInt(int i)
 * \brief Fonction permettant d'afficher le nombre des dixaines et de
 *        l'unité d'un entier sur l'écran.
 * \param L'entier à afficher.
 * \return void.
 */
void LCD_PrintInt(int i){
   char str[3] = "00V";
   int decim = (int) i/10;
   int unit = (int) i%10;
   str[0] = 0x30 | (decim+'0');
   str[1] = 0x30 | (unit+'0');
   LCD_PrintStr(str,3);
}

/**
 * \fn void LCD_Menu(float vmin, float vmax, int cursor)
 * \brief Fonction permettant d'afficher le menu.
 *        Les valeurs de Vmin et Vmax sont affcichées avec le mode auto.
 *        Pour sélectionner une valeur, le curseur clignote sur le point associé
 *        à la sélection en cours.
 * \param Les valeurs de vmin, vmax et la position du curseur (0, 1 ou 2).
 * \return void.
 */
void LCD_Menu(int vmin, int vmax, int cursor){
   LCD_Clear();
   LCD_Home();
   char vmi[5]= "Vmin=";
   char vma[5]= "Vmax=";
   LCD_PrintChar(CHAR_POINT);
   LCD_PrintStr(vmi,5);
   LCD_PrintInt(vmin);
   LCD_transmit_cmd(CURSOR_RETURNLIGNE);
   LCD_PrintChar(CHAR_POINT);
   LCD_PrintStr(vma,5);
   LCD_PrintInt(vmax);
   LCD_PrintChar(' ');
   LCD_PrintChar(CHAR_POINT);
   LCD_PrintStr("Aut", 3);
   LCD_set_Cursor(0, 0);
}

/**
 * \fn void LCD_vmin_menu(float vmin)
 * \brief Fonction permettant d'afficher le menu de sélection de vmin.
 * \param La valeur de vmin.
 * \return void.
 */
void LCD_vmin_menu(int vmin){
   LCD_Clear();
   LCD_Home();
   char ligne1[11] = "Selec Vmin:";
   LCD_PrintStr(ligne1, 11);
   LCD_transmit_cmd(CURSOR_RETURNLIGNE);
   LCD_PrintInt(vmin);
}

/**
 * \fn void LCD_vmin_actualisation(float vmin)
 * \brief Fonction permettant de modifier la valeur afficher de vmin
 *        sans réécrire tout le texte de "LCD_vmin_menu".
 * \param La valeur de vmin.
 * \return void.
 */
void LCD_vmin_actualisation(int vmin){
   LCD_set_Cursor(0,1);
   LCD_PrintInt(vmin);
}
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

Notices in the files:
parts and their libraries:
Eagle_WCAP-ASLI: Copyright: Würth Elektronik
